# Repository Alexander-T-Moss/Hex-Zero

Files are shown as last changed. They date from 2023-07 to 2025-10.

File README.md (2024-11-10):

# &#x2B22; Hex-Zero &#x2B22; 

At its core, HX0 is a re-design of the [Tri-Zero](https://github.com/zruncho3d/tri-zero) Z motion, with a revised [Pandora Gantry](https://github.com/MasturMynd/Pandora). Without the aforementioned, none of this project would've been possible, so a great amount of thanks is due to [zruncho3d](https://github.com/zruncho3d) and [MasturMynd](https://github.com/MasturMynd) whom indirectly sent me down this rabbit hole!

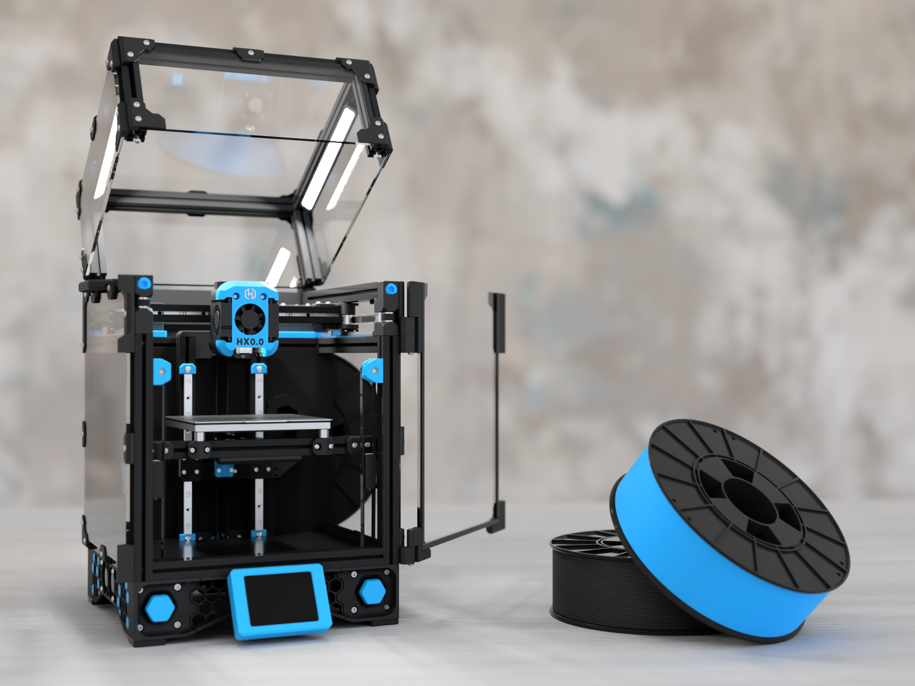
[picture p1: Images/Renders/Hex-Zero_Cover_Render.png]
Hex-Zero_Render


[Latest Release](https://github.com/Alexander-T-Moss/Hex-Zero/releases)

[BOM And Sourcing Guide](https://docs.google.com/spreadsheets/d/1rqf1-H34D0NAQSOrVUcAvukW5k4i_Hs-t34R7qeSDDk/edit?usp=sharing)

~~[Very Early Release Manual](https://docs.google.com/presentation/d/1XJv6mhR6lkI2eAlZ3oS6MfDWln81kRRjcN10jNzyiEM/edit?usp=sharing)~~ (Ignore This, Refer To CAD)

[Common Questions And Answers](https://github.com/Alexander-T-Moss/Hex-Zero/blob/main/QnA.md)

[Community Mods For HX0](https://github.com/Alexander-T-Moss/Hex-Zero/blob/main/Mods)

<br>

## What Differentiates Hex-Zero From Tri-Zero + Pandora Gantry?

When I started working on Hex-Zero, I wanted to address my main concern with Tri-Zero, which was the robustness of the flying bed. I also liked the more honeycomb look of the V0.2 skirts and wanted to incorporate that style into the Hex-Zero skirts. I also noticed some other compatibility issues with how I intended to build things so would need to address them. Below is a summary of some of the major tweaks and changes you'll notice when comparing Hex-Zero to Tri-Zero + Pandora Gantry.

1. Option to either **use bolts** on all bearing stacks **or pins** on all bearing stacks
2. Use **KGLM-03** spherical bearings in the flying bed Z joints (_improve rigidity_)
3. **Reduced Z height of the Z motor mounts** and skirts (_part of the aesthetic changes_)
4. **New front Z tensioners/idlers** to allow clearance with MiniSB (*with additional travel of pandora style gantry*)
5. Optimize printed parts to be **easier to print**
6. **More best-agon hexagons!**

Documentation is another frequently overlooked aspect of projects like these (and by far the most time-consuming thing to complete). When I first started this journey (_before even designing anything_), I had many questions about hardware compatibility, such as "If I do thing A, can I also do thing B", "To do thing C, what do I need for thing D" and "Will doing thing E even work!" To make this project as accessible as possible, I intend to develop documentation and resources that address as many common questions as possible!

<br>

## Community Beta Testing Builds

I want to extend a massive thanks to everyone who took a leap of faith in building and testing this project in its early stages, below is a collage of some HX0s built during the beta testing of this project :)

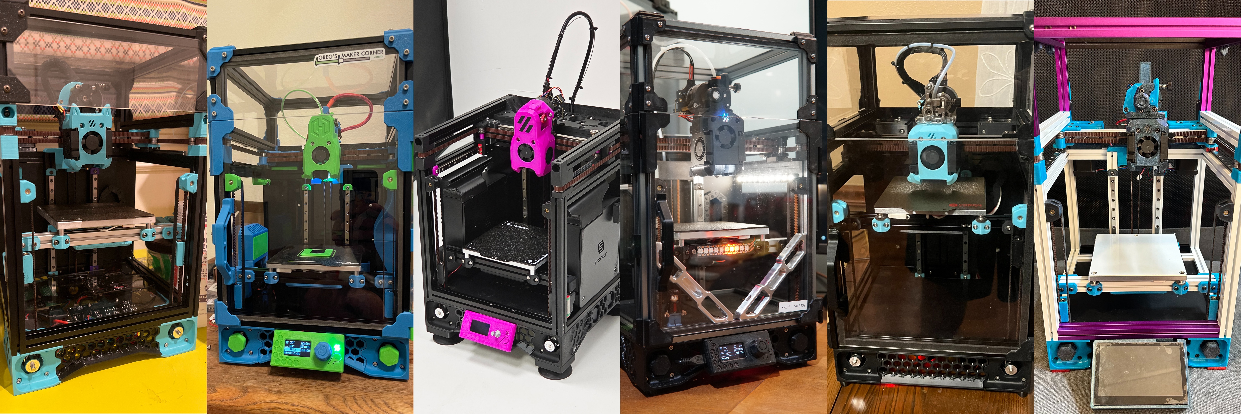
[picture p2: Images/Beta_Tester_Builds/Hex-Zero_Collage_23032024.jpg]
Beta Testing Collage


Credits in order of images left to right: Hud (*HX0.1*),  Rahim Damji (*HX0.2*), Siboor (*HX0.3*), Spicy Pesto (*HX0.5*), Albino Deer (*HX0.4*), Sidjdosjsid (*HX0.ToBe*)

<br>

## Credits

- **[Zruncho3D](https://github.com/zruncho3d)**: Creator of [Tri-Zero](https://github.com/zruncho3d/tri-zero), what started this project
- **[MasturMynd](https://github.com/MasturMynd)**: Designer of the amazing [Pandora's gantry](https://github.com/MasturMynd/Pandora)
- **[Nemgrea](https://github.com/nemgrea)**: For creating [V0.2](https://vorondesign.com/voron0.2), the real root of this project
- **[Chirpy](https://github.com/chirpy2605)**: The brains behind the wonderful [dragon burner](https://github.com/chirpy2605/voron/tree/main/V0/Dragon_Burner) toolhead

If you accidentally stumbled across this project, checkout other similar projects on [3D Printers... For Ants](https://3dprintersforants.com/)

<br>

## Support

With all things, nothing is truly perfect, so if you come across any issues, no matter how small, or find something you think can be improved, please don't hesitate to reach out with suggestions/feedback on the DOOMCUBE discord server in the [dedicated development channel](https://discord.com/channels/825469421346226226/1220161815455989800) for this project!

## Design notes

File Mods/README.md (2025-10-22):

# &#x2B22; Mods & Additions &#x2B22; 

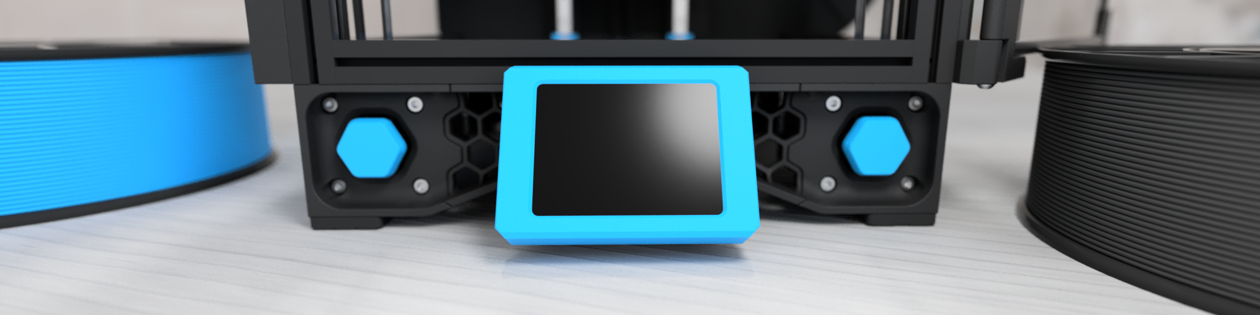
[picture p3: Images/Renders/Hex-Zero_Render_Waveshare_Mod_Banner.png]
Waveshare_Banner_Image


# List Of Mods

| Author | Mod Name | Description |
| --- | --- | --- |
| Alexander T-Moss |  [3mm Panel Clips](/Mods/Alexander_T-Moss/3mm_Panel_Clips) | Allows the use of 3mm foam tape |
| | [Handles](/Mods/Alexander_T-Moss/Handles) | Somewhere to grab onto to lift the printer up |
| | [Full Height Panels](/Mods/Alexander_T-Moss/Full_Height_Panels) | Hard mounted top hat and info on using full height panels (BoxZero esque)|
| | [Bed Fans](/Mods/Alexander_T-Moss/Bed_Fans) | Mounts for 3010 blower fans on the underside of the bed |
| | [Hex Panels](/Mods/Alexander_T-Moss/Hex_Panels) | For if you want more bestagons in your printer |
| | [Skirt Fans](/Mods/Alexander_T-Moss/Skirt_Fans) | Mounts for a pair of 3010's on the side skirts |
| MechaXx |[Waveshare 2.8 Screen](/Mods/MechaXx/Waveshare_28_Screen) | Waveshare 2.8 screen front skirt mount |
| tiramisu |[Serial Plates](/Mods/tiramisu/Serial_Plates) | HX0 Serial Plate for 1515 extrusions |
| Hoeby |[Bottom Wago Holder](/Mods/Hoeby/Bottom-Wago-holder) | Wago Block Holder |
| | [Bottom FT EMS](/Mods/Hoeby/Bottom_FT_EMS) | Bottom FT EMS |
| | [Front belt tensioner](/Mods/Hoeby/Front_Belt_Blocks) | Different belt clamping in front tensioner |
| | [Extended MantaRay kinematic](/Mods/Hoeby/MantaRay%20mount%20with%20extend) | Prevent easelly dropping MantaRay |
| | [HX0_Anthead](/Mods/Hoeby/HX0_Anthead) | AntHead with mods specially for HX0 |
| | [PurgeBucket](/Mods/Hoeby/PurgeBucket) | PurgeBucket to fit Mantaray and Hammerhead bed |
| | [SuperSlicer](/Mods/Hoeby/SuperSlicer_Texture_Model) | Files to customize your SuperSlicer to HexZero |
| | [MantaRay KGLM03 joints](/Mods/Hoeby/MantaRay%20with%20KGLM03%20joints) | MantaRay bed with KGLM03 ball joints |
| MJ26gaming | [4010 Bed Fan](/Mods/MJ26gaming/Hex%204010%20Bed%20Fan) | Mount for dual 4010 bed fans |
| G |  [Hex-Burner Revo PZ](/Mods/G/Hex-Burner_Revo_PZ) | STLs for routing and mounting the Revo PZ |
| |  [Hex-Burner Offset Carriage](/Mods/G/Hex-Burner_Offset_Carriage) | X-Carriage to offset the Hex-Burner toolhead 2mm forward |
| |  [Top Hat Braces](/Mods/G/Top_Hat_Braces) | A collection of STLs to permanantly secure the top hat |
| |  [GBB15 Motor Panel](/Mods/G/GBB15_Motor_Panel) | GBB15 motor panel mount |
| fronti90 |[48mm Z Motors](/Mods/fronti90/48mm_z_motors) | Mounts and skirts for 48 mm Z Motors |

<br>
<br>
<br>

# Information For Adding A Mod
Below is a quick summary of changes required for submitting a mod to the mods folder

## Table Structure
Information for updating the table for the addition/modification of a mod
- Put the name of the mod hyperlinked to the location of the mod in the repo
- A short single-sentence description of the mod
- Your name as the author

Example table entry: `| Your Name Here |  [Mod Folder Name](Link_To_Mod_Folder) | Short Description |`

## Folder Structure
Information for updating the `Mods` folder for the addition/modification of a mod

The `Mods` folder uses a 2 layer folder structure to organize all the mods
1. `Author Folder` - Top-level folder where all of an author's mods are
2. `Mod Folder` - The folder for an individual mod, which will be found in its relevant `Author Folder`

### Example Of Mod Folder Structure

| `Mods` Folder | `Author Folder` | `Mod Folder` |
| --- | --- | --- |
| Mods | Person 1 | Mod A From Person 1 |
|  |  | Mod B From Person 1 |
|  |  | Mod C From Person 1 |
|  | *Person 2 | *Mod D From Person 2 |
|  | Person 3 | Mod E From Person 3 |
|  |  | Mod F From Person 3 |

_*Note: If someone has a single mod it still has an author folder_

## What Must A Mod Folder Need To Include
At a bare minimum, each mod folder should contain a CAD file (_ideally a .step and/or .f3d file_), STLs (_ideally oriented correctly for printing_) a **screenshot from CAD or a photo** of the mod installed and a short `README.md` providing the relevant information for the mod

Also, make sure there are no spaces in any file or folder name (_using underscores `_` or dashes `-` where required_)

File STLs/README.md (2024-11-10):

# &#x2B22; Printing Guide &#x2B22; 

Below you'll find information on recommended print settings, how to slice MMU parts, etc.

<br>

## Recommended Print Settings
All printed parts where possible are designed with the following print settings in mind.

> Material: `ABS/ASA` (_Or Better_)
>
> Perimeters: `4`
>
> Top/Bottom Layers: `5`
> 
> Infill: `40% Cubic`
> 
> Layer Height: `0.2mm` (_Incl. First Layer_)
> 
> Extrusion Width: `0.4mm Forced` (_Just For Internal/External Perimeters_)

<br>

## Optional Multi-Material Parts
Where applicable, there are `.step` files for parts that can be printed in multiple colours. They are often located in a folder of the part name along with an `.stl` of the part.

> After importing them into your slicer of choice, if they don't already show as multiple parts, right click on the object and split it into parts (not objects!).
>
> Also worth noting the `.step` version of parts are not oriented so you may need to refer to the `.stl` for correct orientation.

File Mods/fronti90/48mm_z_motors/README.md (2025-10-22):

# &#x2B22; 48mm Z Motors &#x2B22;
Mounts and skirts for 48 mm Z Motors (e.g. 17HS19-2004S1)

Additionally you will need to change your electronics setup. For me mounting the PSU at the bottom (at an angle) and all other electronics on the back worked best.

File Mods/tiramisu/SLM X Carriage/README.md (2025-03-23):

# HexMetal
Toolhead carriage designed for SLM printing and use in the Hex Zero printer for ants or any other front-facing MGN9H rail printer.

This is heavily based on the **incredible** work Alex has done designing the Hex Zero.

~~Currently awaiting the first prototype by PCBWay :)~~
~~Received, belt path needs to be widened but all else is OK. New ETA: When I receive and test new part :)~~

Revised version received and test fitted. Minor tweaks made based on use.
Files have now been uploaded. **Highly advised** that you print in FDM first and consider how SLM tolerances would change the fit you get.

I have uploaded version with both a mounting for normal Dragonburner (and similar) as well as Alex's Dragonburner for Hex Zero.

This render is not fully indicative of the STLs, will update soon.

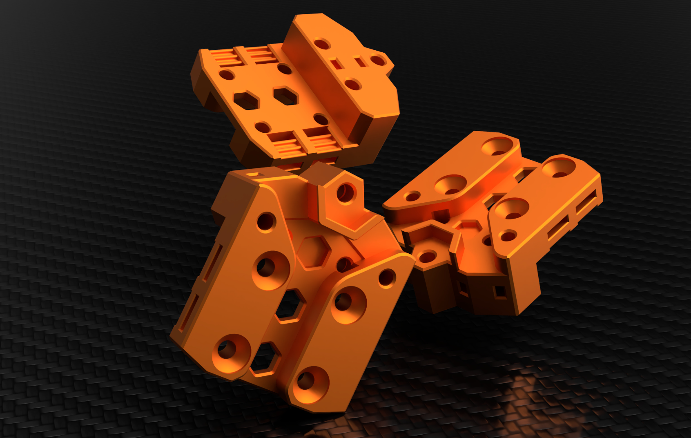
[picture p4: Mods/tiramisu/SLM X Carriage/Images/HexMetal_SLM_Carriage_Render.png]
Render of HexMetal, same part, shown thrice from different angles


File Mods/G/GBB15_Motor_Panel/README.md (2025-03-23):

# GBB15 Motor Panel Mount

This mod mounts the GBB15 in place of the motor panel. The board is mounted so that the MCU and motor drivers can be heat sinked into the chamber. The Bowden tube and CAN harness can be zip tied in place through the hexagon hole into the chamber. Two M3 heatset inerts are required mount the GBB15 to the panel.

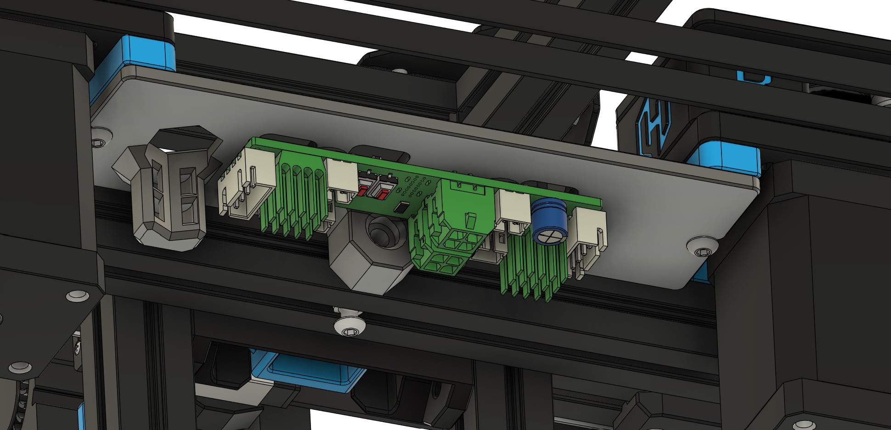
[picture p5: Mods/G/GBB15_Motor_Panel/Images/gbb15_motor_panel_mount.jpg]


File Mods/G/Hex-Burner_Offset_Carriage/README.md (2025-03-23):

# Offset X-Carriage for Hex-Burner

This mod offsets the placement Hex-Burner toolhead 2mm forward. A support piece is included in the STL, and can be removed after printing.

The intent of offsetting the toolhead is for: 
- Routing of all toolhead wires in the carriage channel.
- Clearing the Pi Camera with using the popular Voron 0 Raspberry Pi Camera Mount by johanncc. Depending on the size of the camera PCB, the mount corner of the PCB may need to be trimmed. 
- Allowing excees belt to extend out the side of the carriage without affecting toolhead alignment. 

The disadvantage to this mod is that you will lose 2mm of Y-axis travel; however, this is negligible in many cases, especially if you are using the mini-fridge door mod.

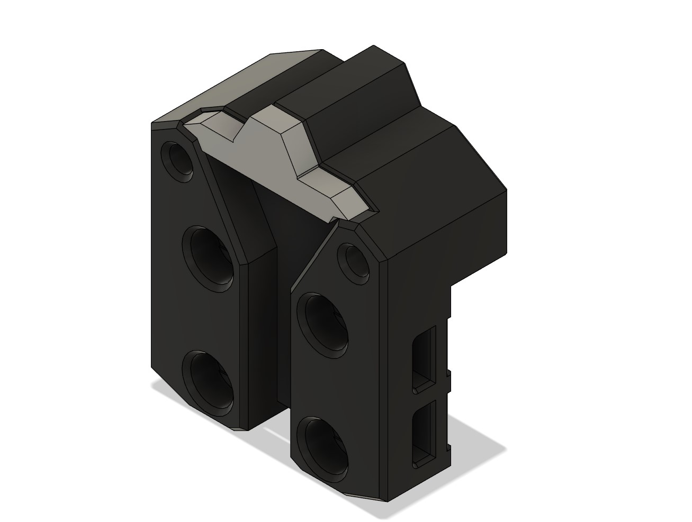
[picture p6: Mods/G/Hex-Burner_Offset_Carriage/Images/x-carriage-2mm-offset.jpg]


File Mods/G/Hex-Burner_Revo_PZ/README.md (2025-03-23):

# Revo PZ Mods for Hex-Burner

This is a set of STLs to use the Revo PZ with the Hex-Burner. 

## Hex-Burner Revo PZ Sherpa Mount
The Revo PZ Sherpa Mount is used to provide a routing path of the PZ's flex cable through the top and out of the back of the toolhead. This part is compatible with the Hex-Burner's fastener spacing and any Sherpa style extruder.

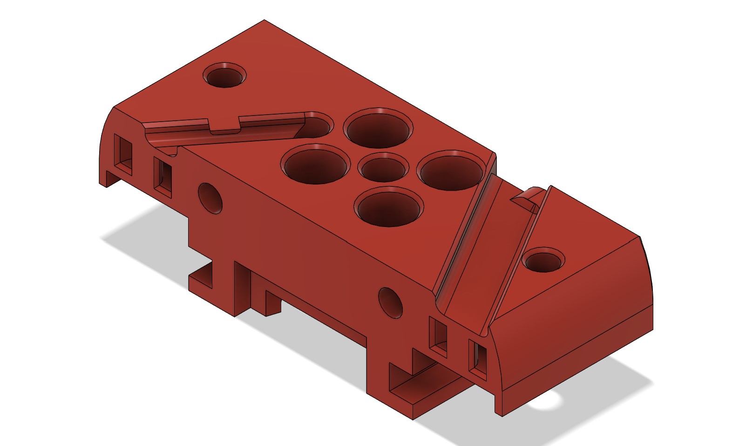
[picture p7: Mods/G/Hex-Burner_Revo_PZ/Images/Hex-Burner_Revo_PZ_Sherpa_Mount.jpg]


## X-Carriage Revo PZ Board Mount
The X-Carriage Revo PZ Board Mount is used to mount the PZ's breakout board on top of the Hex-Burner X-Carriage and under the extruder motor. Optionally, there is a version with an extended X-axis bumper and zip-tie point for the hot end wires. The bumper is placed to impact the XY joints during sensorless homing. This mount will require the top toolhead screw to be 2mm longer. Two M3 heatset inerts can be added for an attachment point with toolhead MCU mounts. The image below shows the Maple Leaf Makers EBB36 interfacing with this mount.

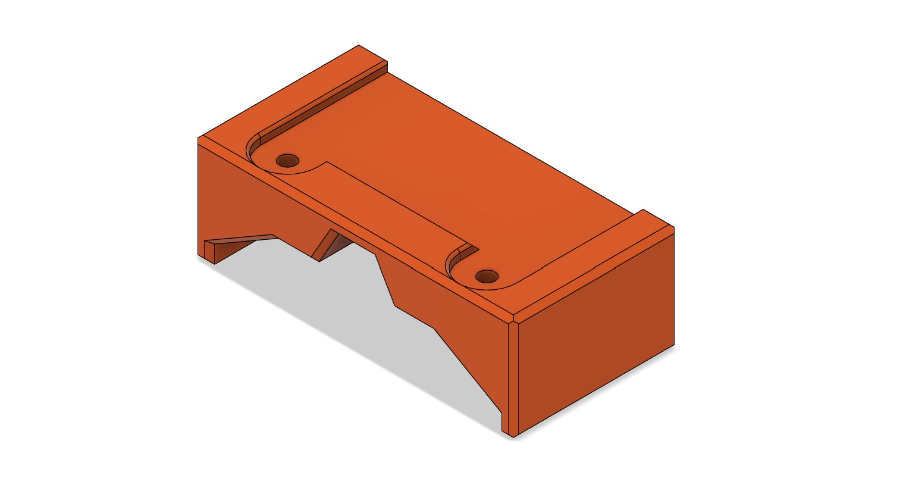
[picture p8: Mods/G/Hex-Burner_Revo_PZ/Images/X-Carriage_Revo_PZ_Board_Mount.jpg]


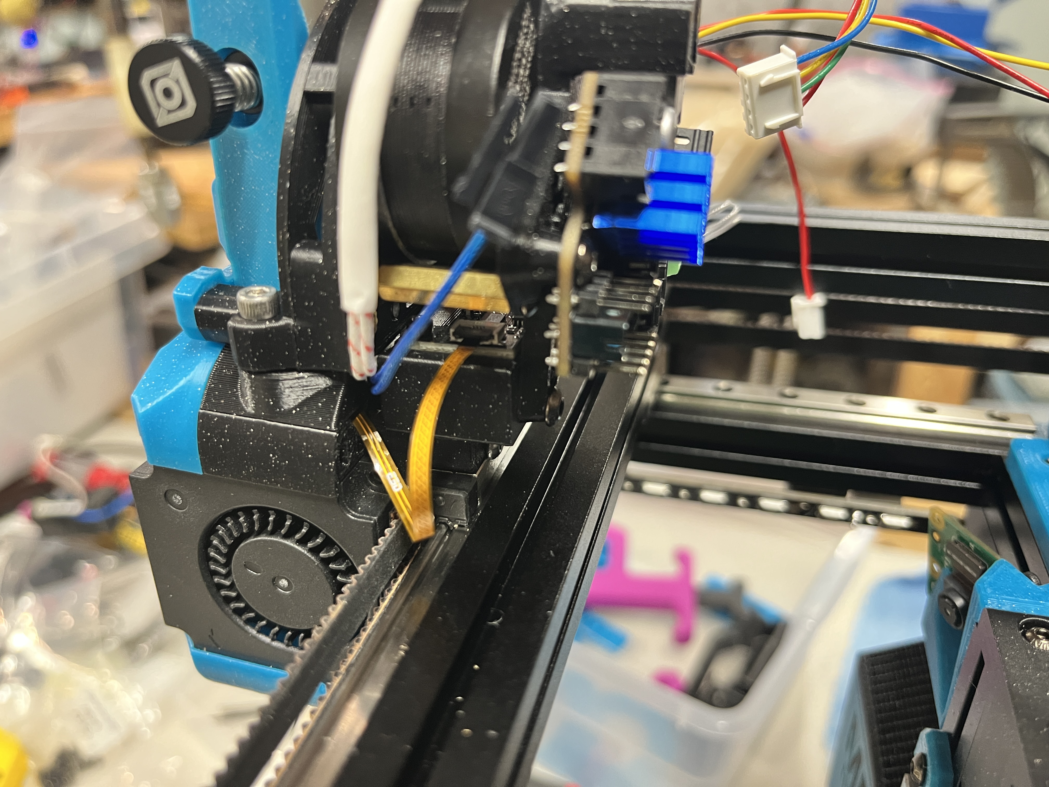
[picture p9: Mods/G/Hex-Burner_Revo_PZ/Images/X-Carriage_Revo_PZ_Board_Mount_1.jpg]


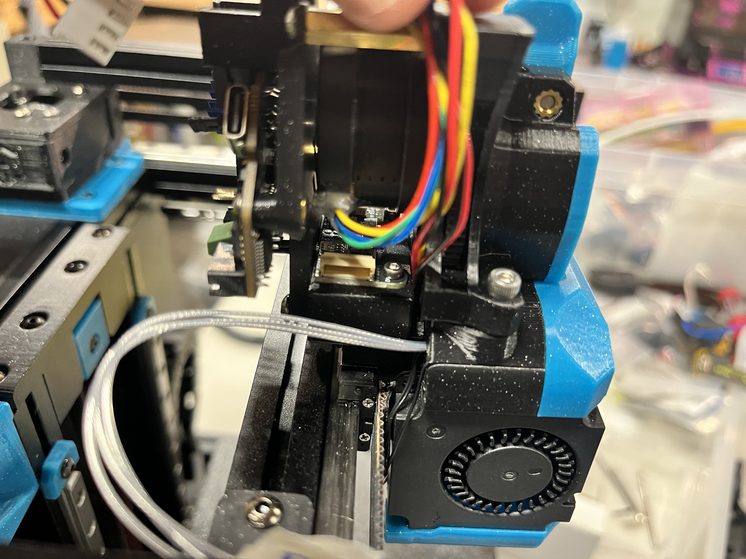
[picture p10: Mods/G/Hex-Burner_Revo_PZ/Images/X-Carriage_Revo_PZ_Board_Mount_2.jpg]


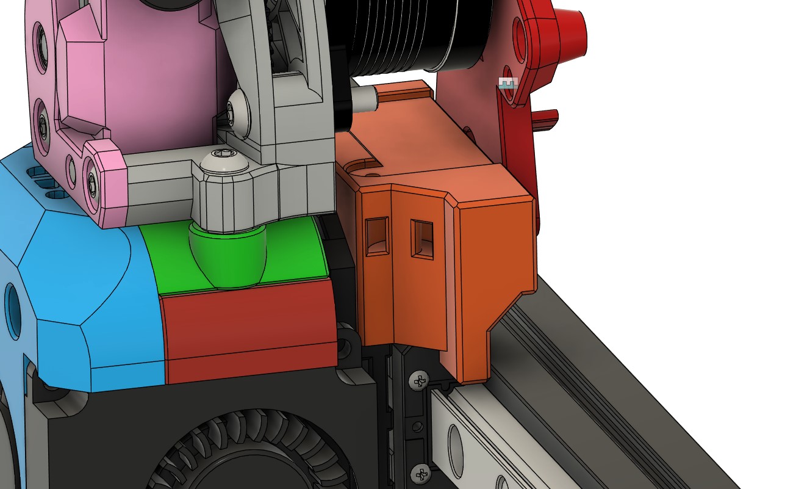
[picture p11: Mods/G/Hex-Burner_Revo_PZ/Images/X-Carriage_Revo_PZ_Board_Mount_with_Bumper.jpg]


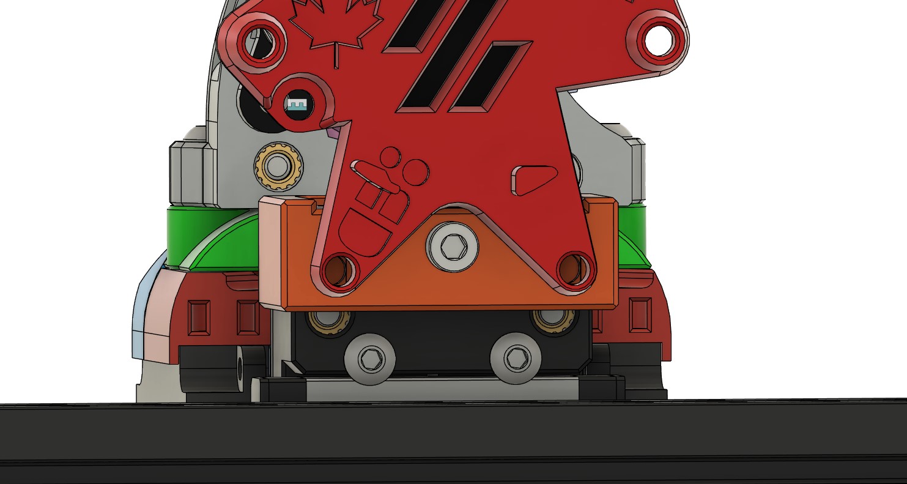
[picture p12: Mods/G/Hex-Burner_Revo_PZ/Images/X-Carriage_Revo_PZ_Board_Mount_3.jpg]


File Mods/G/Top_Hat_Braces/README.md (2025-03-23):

# Top Hat Braces

This mod is a colletion of STLs to secure the top had to the printer.

The corner brace with 2mm offset can be used for mini-fridge mod users needing to extend the height of the top hat. Additional nuts will need to be preloaded into the top hat extrusions.

The rear brace interfaces with existing mount points and had a slot for the Voron0 rear panels.

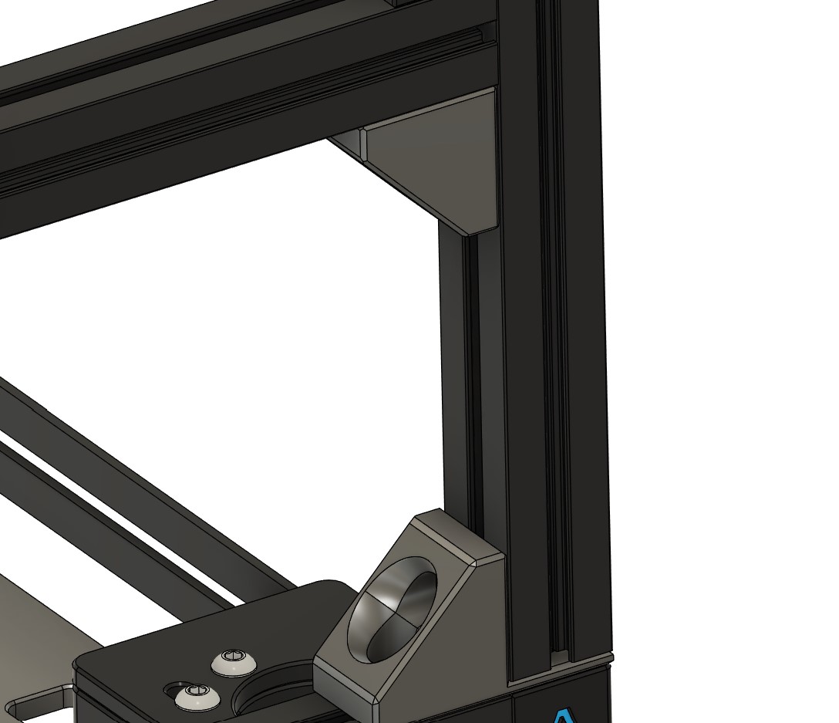
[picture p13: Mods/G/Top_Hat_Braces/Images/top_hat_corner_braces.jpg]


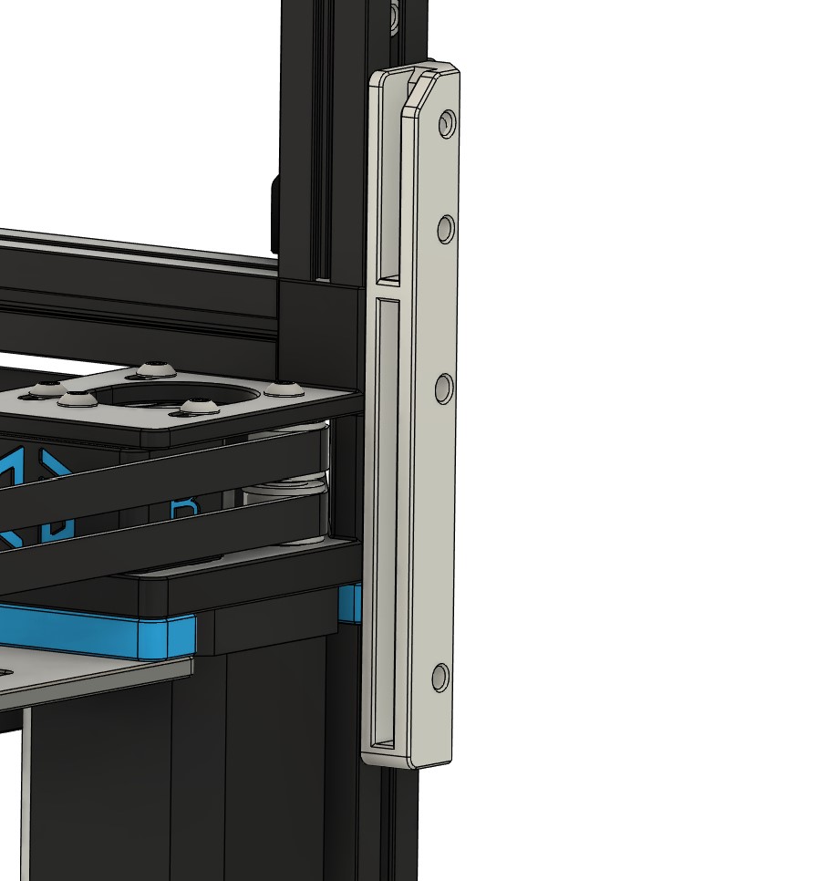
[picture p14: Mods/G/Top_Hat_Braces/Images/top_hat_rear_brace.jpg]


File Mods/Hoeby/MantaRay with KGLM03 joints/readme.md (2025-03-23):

# &#x2B22; HX0 MantaRay bed with KGLM03 ball joints &#x2B22;
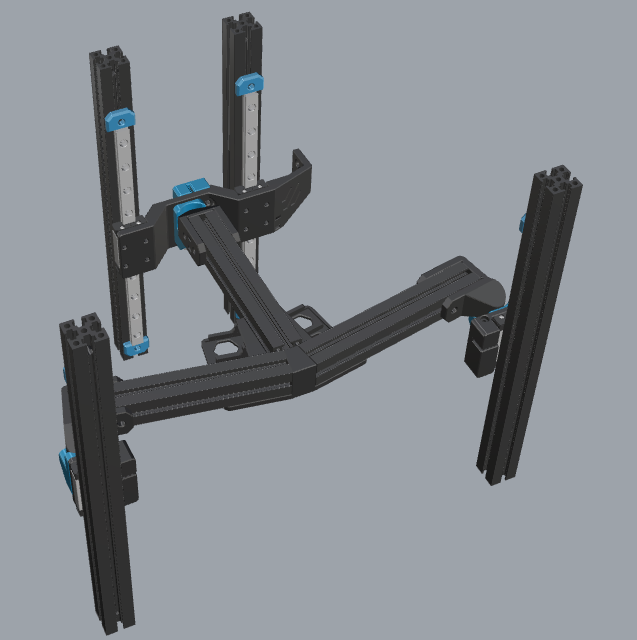
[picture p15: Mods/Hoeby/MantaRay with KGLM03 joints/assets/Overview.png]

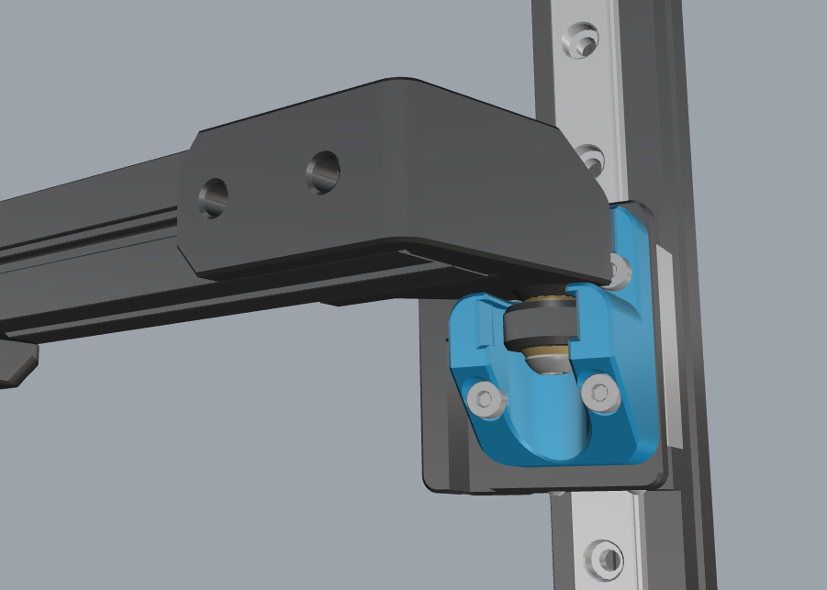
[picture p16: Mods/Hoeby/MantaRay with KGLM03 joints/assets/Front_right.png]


# Mod Guide
The MantaRay uses the stock 3x 100mm extrusions from a V0 kit. <br>
Original the MantaRay uses rail mounts with pins, they are easier to source then the KGLM03 joints. <br>
This mod uses the KGLM03 joints from the Hammerhead bed, on the MantaRay bed.

## What are the changed parts in this mod:
- [a]_kinematic_rail_front_left.stl
- [a]_kinematic_rail_front_right.stl
- [a]_kinematic_rail_rear.stl
- front_left_gantry_attachment.stl
- front_right_gantry_attachment.stl
- rear_gantry_attachment.stl

## Needed parts
- 3x KGLM-03
- 2x M2x8
- 4x M2x10
- 2x M2x15
- 4x M2x16
- 3x M3x10
- 3x Heat insert (voron size)

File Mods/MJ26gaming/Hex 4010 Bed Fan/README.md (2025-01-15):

# Dual 4010 Axial Bed Fan Mount for Hex Zero

## About this mod
This replace's the mod Alexander made, allowing for even more CFM for chamber heating. <br>
It definitely works with the Hammerhead bed. I have not tested it on the Manta Ray but it probably works there too. <br>
I use GDStimes, I will update with the lifespan of those. <br>
Consider usinga stronger bed heater. The BOM 60w heater will definitely be overcooled by this. I use a 120w heater.

## Filament
I reccomend using you highest temp filament for this. <br>

## Hardware needed for this mode
- 2x M3x8
- 8x M3x12
- 8x M3 Heatset Inserts

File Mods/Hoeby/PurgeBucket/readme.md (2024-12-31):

# PrugeBucket for HexZero, mantaray and hammerhead bed compatible
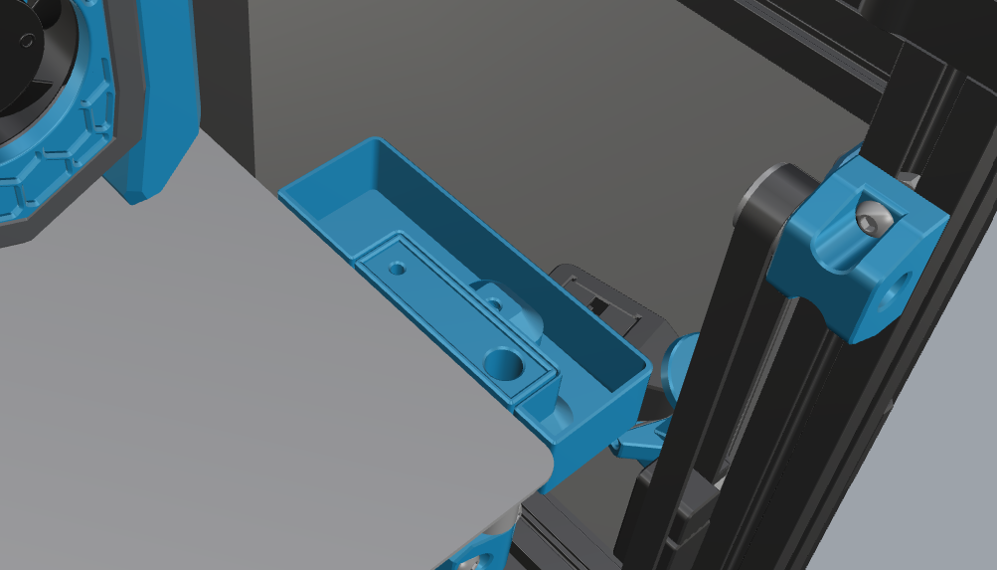
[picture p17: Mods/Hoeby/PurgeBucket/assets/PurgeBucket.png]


## Which 3d parts are shared
Only the 3D printed parts for the PurgeBucket are shared. <br>
The bed-mount is mantaray and hammerhead bed compatible.

## Hardware needed for this mode
- 2x M3x8
- 2x M3 nut
- 2x Magnet 6x3
- 1x Nozzle silicone brush (Bambu A1)

## Printing advice
The advice is to print the bucket with support. <br>
There isn't a drawn support in the file. <br>
Without a support, the magnet hole for the bucket could be deformed.

## Used klipper macro
This macro is used to clean the nozzle. <br>
```
[gcode_macro CLEAN_NOZZLE]
variable_start_x: 128
variable_start_y: 55
variable_start_z: 3.6
variable_wipe_dist: 45
variable_wipe_count: 5
variable_wipe_speed: 10000
variable_raise_distance: 20

gcode:
 ## Check if extruder has minimum extrude temperature, otherwise heat extruder
 {% set temp_to_low = False %}
 {% set temp_min = printer.configfile.settings["extruder"].min_extrude_temp|float %}  

 ## Check if the target that is set on the extruder is larger then minimum extruder temp
 ## Otherwise heatup to minimum extruder temp
 {% if printer.extruder.target < temp_min %}
    M104 S{temp_min}
    {% set temp_to_low = True %} 
 {% endif %}
 
 ## Check if homing is done, otherwise homing
 {% if "xyz" not in printer.toolhead.homed_axes %}
   G28
 {% endif %}

 ## Check if Z_Tilt is done, otherwise Z_Tilt_Adjust
 {% if printer.z_tilt.applied == False %}
   Z_TILT_ADJUST
 {% endif %}

 ## There was no extruder target, waiting for extruder to finish heating to minimum extruder temp
 {% if temp_to_low == True %}
   M109 S{temp_min} 
 {% endif %}

 G90                                            

 ## Move nozzle to start position
 G1 X{start_x} Y{start_y} F{wipe_speed / 2}
 G1 Z{start_z} F1500

 ## Wipe nozzle
 {% for wipes in range(wipe_count) %}
    {% for coordinate in [(start_x, start_y),(start_x, start_y - wipe_dist)] %}
        G0 X{coordinate[0] - 0.6 * wipes} Y{coordinate[1]} F{wipe_speed}
    {% endfor %}
 {% endfor %}

 ## There was no extruder target, disable extruder heater
 {% if temp_to_low == True %}
   M104 S0 
 {% endif %}
  
 ## Raise nozzle
 G1 Z{raise_distance} F1500
 G1 X60 Y60 F{wipe_speed / 2}

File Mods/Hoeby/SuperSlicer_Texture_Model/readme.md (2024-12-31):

# HexZero texture and model for SuperSlicer
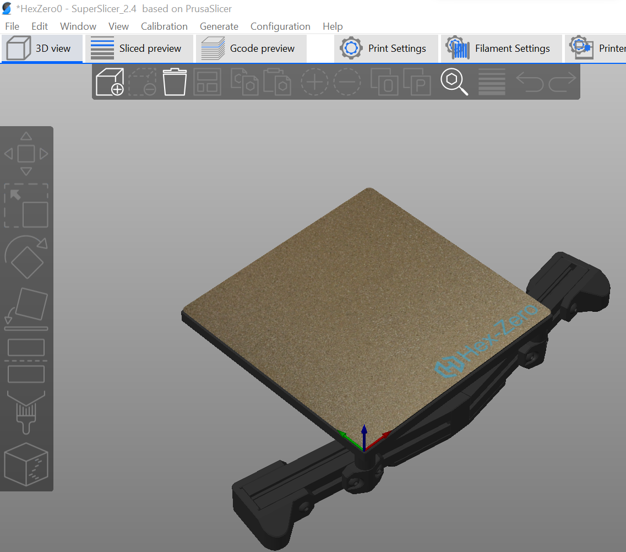
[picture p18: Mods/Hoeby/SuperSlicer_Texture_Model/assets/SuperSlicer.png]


This is not a 3d mod, but files to import the HexZero into your SuperSlicer <br>

## How to change to bed + sheet in SuperSlicer
- Open SuperSlicer <br>
- Go to <b>Printer settings</b>
- Choose <b>General</b>
- Choose <b>Set</b>
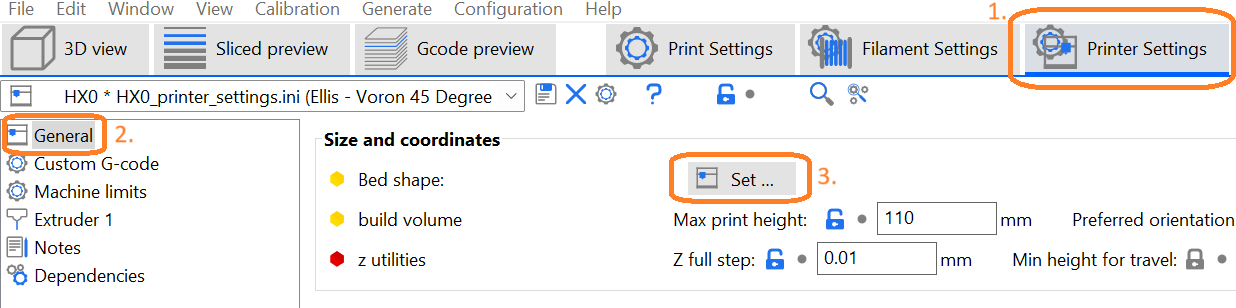
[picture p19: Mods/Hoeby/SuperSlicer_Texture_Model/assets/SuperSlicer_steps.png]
 <br>
<br>
- A option <b>Texture</b> choose <b>Load</b> and search for the .png file <br>
- A option <b>Model</b> choose <b>Load</b> and search for the .stl file <br>
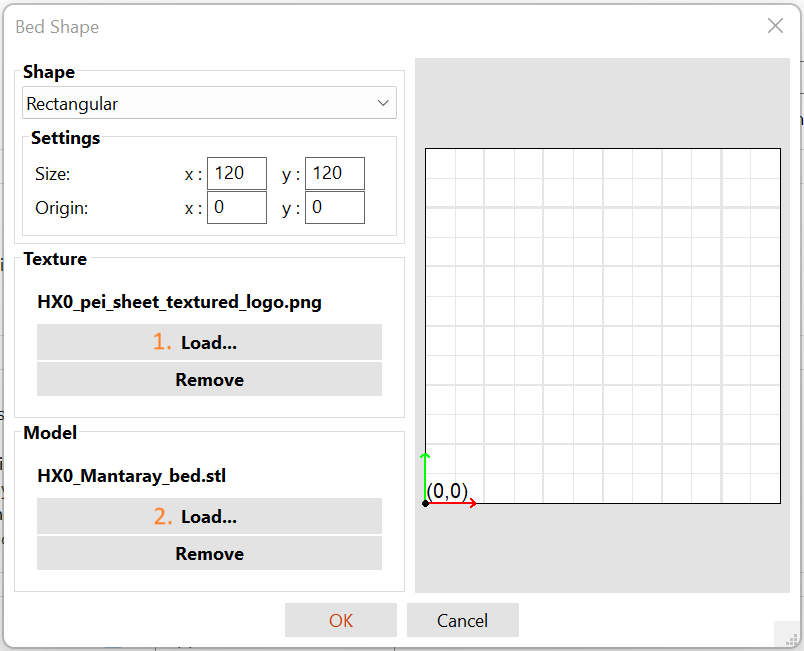
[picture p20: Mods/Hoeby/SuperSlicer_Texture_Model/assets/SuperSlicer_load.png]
 <br>

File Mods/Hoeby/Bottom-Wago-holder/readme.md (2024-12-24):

# Wago-mount special for HexZero

## The idea about this mod
There a nice space next the the Z-extrusions, which this mod will fill up with a wago mount. <br>
The holder has place for:
- 2x Wago 3-pin
- 2x Wago 5-pin

## Which 3d parts are shared
Only the 3D printed parts for the wago-mount are shared. <br>

## Hardware needed for this mode
- 2x M3x8
- 1x M3 nut

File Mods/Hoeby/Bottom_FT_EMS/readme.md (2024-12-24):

# FT_EMS_Bottom special for HexZero

## The idea about this mod
The idea is found here; https://www.printables.com/model/553387-ft-ems-voron-v02-v2-electronics-management-system <br>
Just made it compatible for the bottom of the HexZero

## Which 3d parts are shared
Only the 3D printed parts for the EMS bottom are shared. <br>

## Hardware needed for this mode
- 14x M3x8
- 10x M3 nut

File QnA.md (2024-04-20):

# &#x2B22; Questions And Answers &#x2B22;
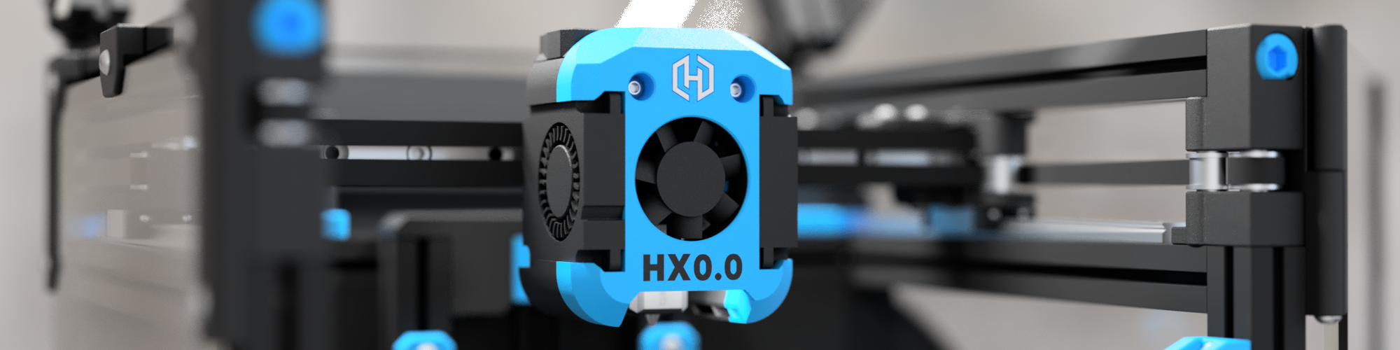
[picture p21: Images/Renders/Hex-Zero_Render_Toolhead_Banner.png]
Hex-Zero_Banner_Image


## How Much Does It Cost To Convert My V0 To A HX0?
Approximately **£100/$125/€115** to **£150/$190/€175**. You may be wondering why there is such a wide range. The cost is entirely dependent on what you already have and how Gucci you want to be when purchasing parts, but you can convert a V0 to a HX0 for somewhere in this range (_conservative estimate_), if not less!

## What Probe Should I Use With My HX0?
There are a few probe options to choose from, all with pros and cons and options depending on what tool head you are using but all need the same general considerations when deciding what is best for your HX0 build!

1. Where is the probe going to dock (_if applicable_)? - Ideally, the dock should put the probe out of the way of the tool head during normal printing. Thanks to the additional XY travel from the Pandora-style gantry in HX0, you get a bit more freedom in probe dock placement. I recommend using a probe mount dock that situates the probe in the rear left corner (_looking into the printer_)

2. How does the probe attach to the tool head (_if applicable_)? Will the additional parts for where the probe attaches to the tool head cause areas where parts will collide when the tool head moves? The main area to pay consideration to is the rear vertical z extrusions. You can often configure the printer in a way to avoid this area to prevent a possible collision

Below is a table detailing some probe and dock combinations and a short pro/con summary for them

| Toolhead Compatibility | Probe | Dock | Pro | Con |
| --- | --- | --- | --- | --- |
| DB & MiniSB | [Klicky]() | [Multple Options](https://github.com/jlas1/Klicky-Probe/tree/main/Printers/Voron/v0#probe-dock-mounts-1) | Well-Documented and community tested | May reduce useable print area and requires homing to front left corner |
|  | [SlideSwipe](https://github.com/chestwood96/SlideSwipe) | N/a | No issues with travel restrictions/collisions | More complex than other probes and needs additional hardware |
| DB Only | [ZeroClick](https://github.com/zruncho3d/ZeroClick?tab=readme-ov-file) | `Centre` | Nice dock position | Toolhead mount may collide with rear z verticle extrusions |

It's also worth noting that HX0 is designed and tested with DB in mind and not MiniSB, so your mileage with MiniSB may vary. Also, each of the recommended probe's pro/cons above assumes using the DB cowl with its respective probe mount

## Do I Need To Buy Extra Extrusion?
Technically, no, but I dislike wording things like that, so allow me to explain. 

If you have a V0 with an extrusion bed, you can build the flying bed using the stock V0 bed extrusions and a printed placeholder at the back of the printer. However, LDO has begun shipping kits with a kirigami and no bed extrusions, which means you will need to source at least one 100mm and one 200mm (or just three 100mm) extrusions for the flying bed in this case, as well as an additional 200mm extrusion for the printer's rear or use the printed place holder.

All that being said, the stock V0 extrusion bed is made up of three 100mm extrusions, and ideally, you want to use a single 200mm instead of two 100mm on the front of the flying bed, so you may still need to source 200mm extrusions for the flying bed and while you're at it, get one for the back of the printer. I should also clarify that the additional rear extrusion is not structural and is only there to make mounting skirts easier at the back of the printer!

Fortunately, these additional extrusions are in lengths that can typically be found pre-cut and tapped

## Do I Need To Drill Holes In The Existing V0 Extrusions?
If you want to mount the rear extrusion, drill two holes to accommodate it. With the printed placeholder, however, you can avoid drilling holes, but I strongly advise you to drill the necessary holes.

There is a jig included to drill the holes, making it rather simple, and because these holes are only to allow an Allen key through to tighten a blind joint bolt, they do not need to be accurate, so there is no need to go for sub-mm or anything silly precise with them!

## Can I Serial A HX0 As a V0?
**Yes**. HX0s can be serialised as a V0 (_assuming you are not converting an existing serialised V0_) while also receiving a HX0 serial to display on the printer!

# Still Got Questions?

Please feel free to reach out on the [dedicated development channel](https://discord.com/channels/825469421346226226/1220161815455989800) for this project in the doomcube discord server!

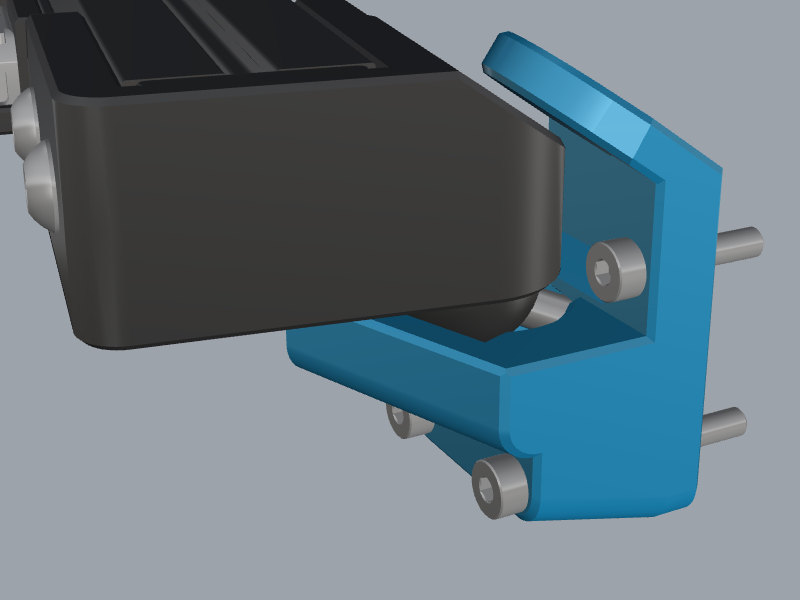
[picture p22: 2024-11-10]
Mods/Hoeby/MantaRay mount with extend/assets/Front Left image.png

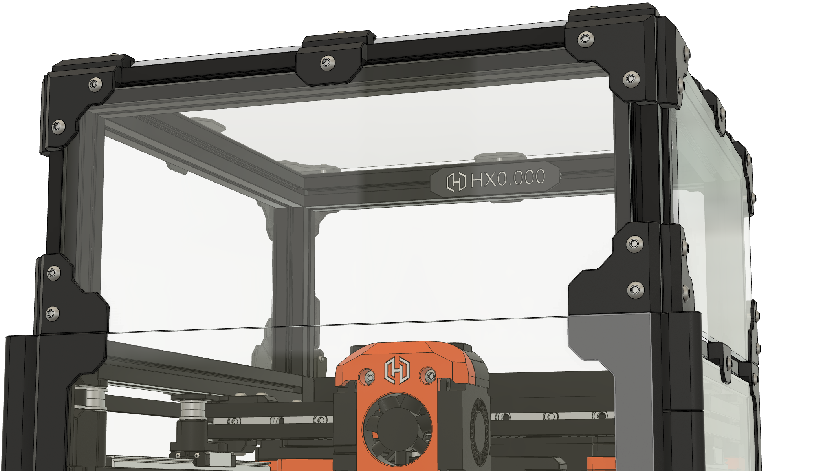
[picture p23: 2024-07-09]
Mods/tiramisu/Serial_Plates/Images/Hex-Zero_Render_Serial_Plate.png

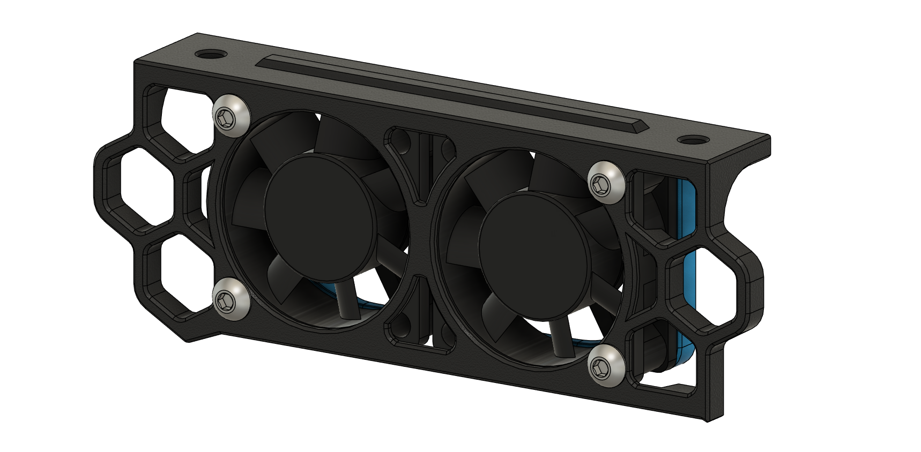
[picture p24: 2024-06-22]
Mods/Alexander_T-Moss/Skirt_Fans/Images/Skirt_Fans.png

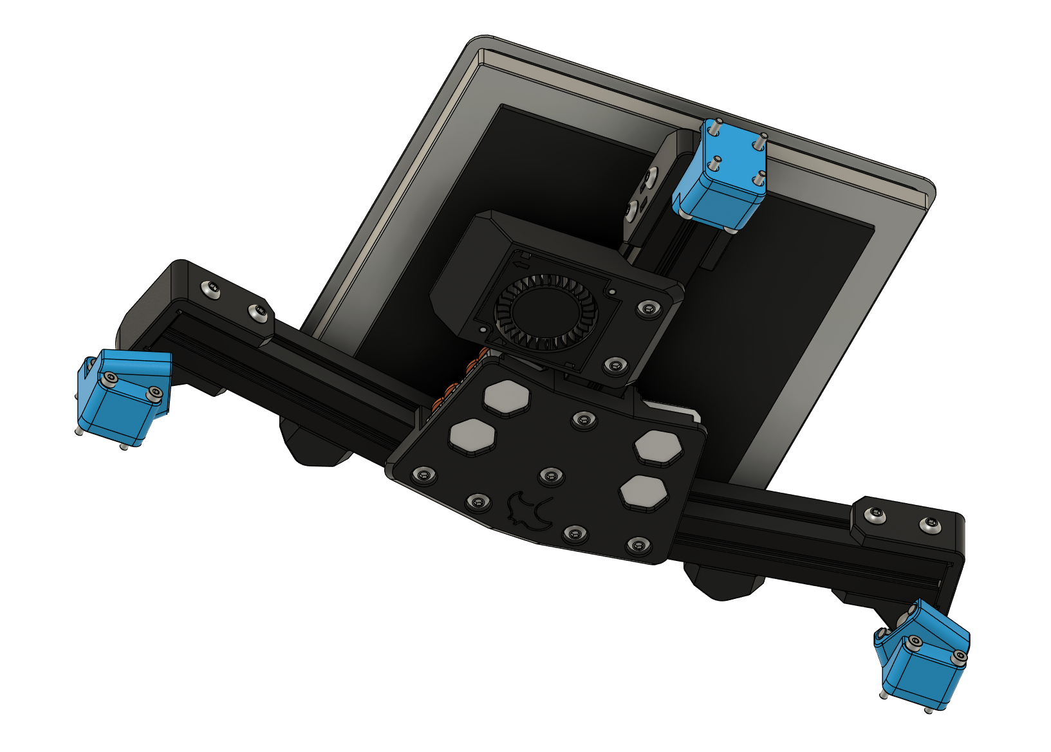
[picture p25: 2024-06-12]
Mods/Alexander_T-Moss/Bed_Fans/Images/single_fan_rear.png

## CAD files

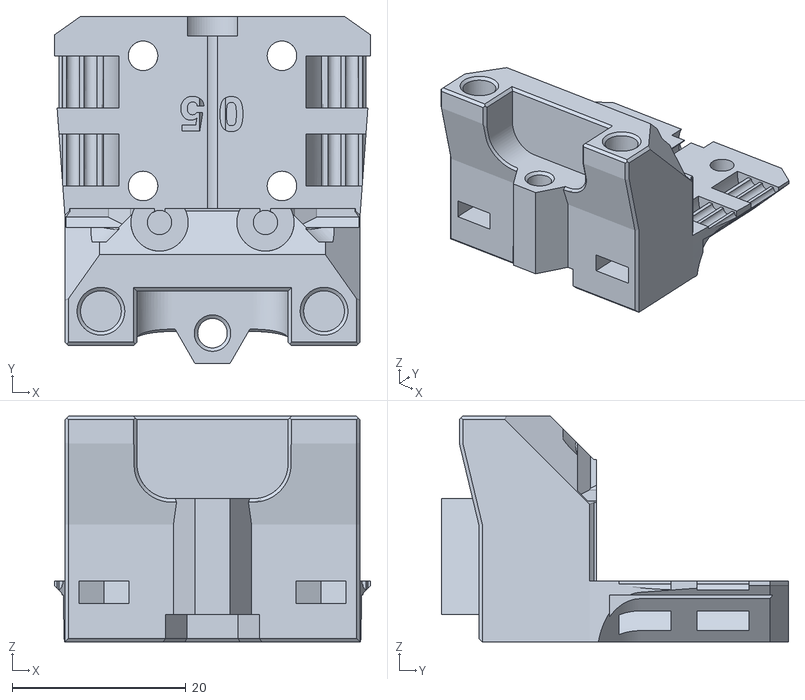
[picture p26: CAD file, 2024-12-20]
Mods/Hoeby/HX0_Anthead/STLs/Carriage/HX0_AntHead_Assembly_v43_x_carriage_x1.stl
36.4 x 40.0 x 26.0

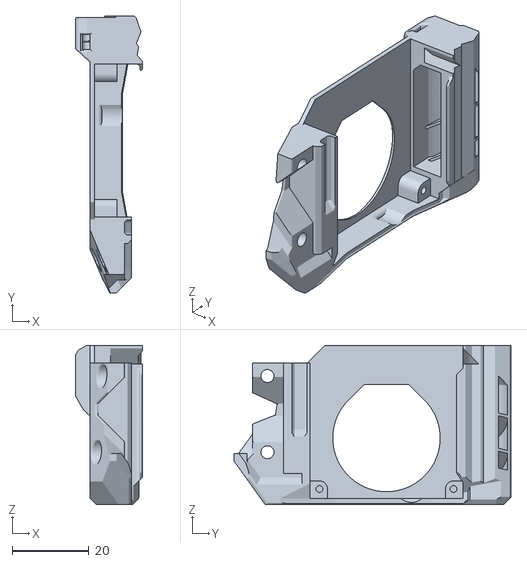
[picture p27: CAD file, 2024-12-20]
Mods/Hoeby/HX0_Anthead/STLs/Ducts/[a]_HX0_AntHead_Assembly_v43_left_duct_x1.stl
17.6 x 72.3 x 41.6

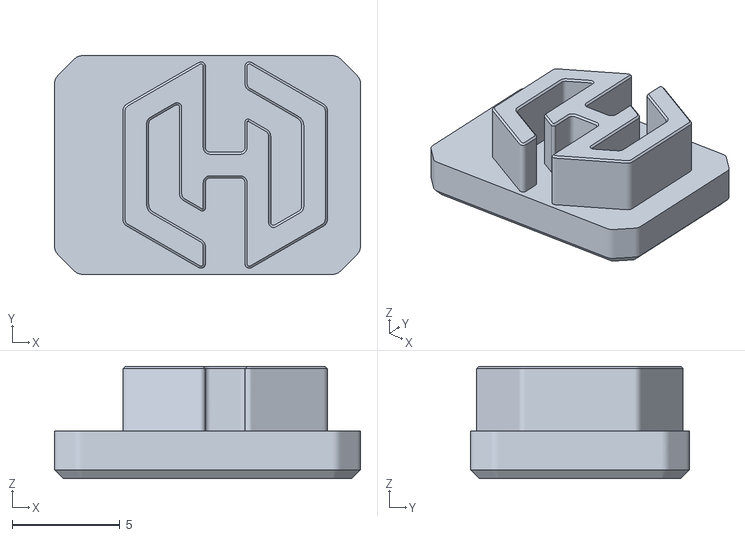
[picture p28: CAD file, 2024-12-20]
Mods/Hoeby/HX0_Anthead/STLs/LEDs/HX0_AntHead_Assembly_v43_led_diffuser_x1.stl
14.2 x 10.1 x 5.20

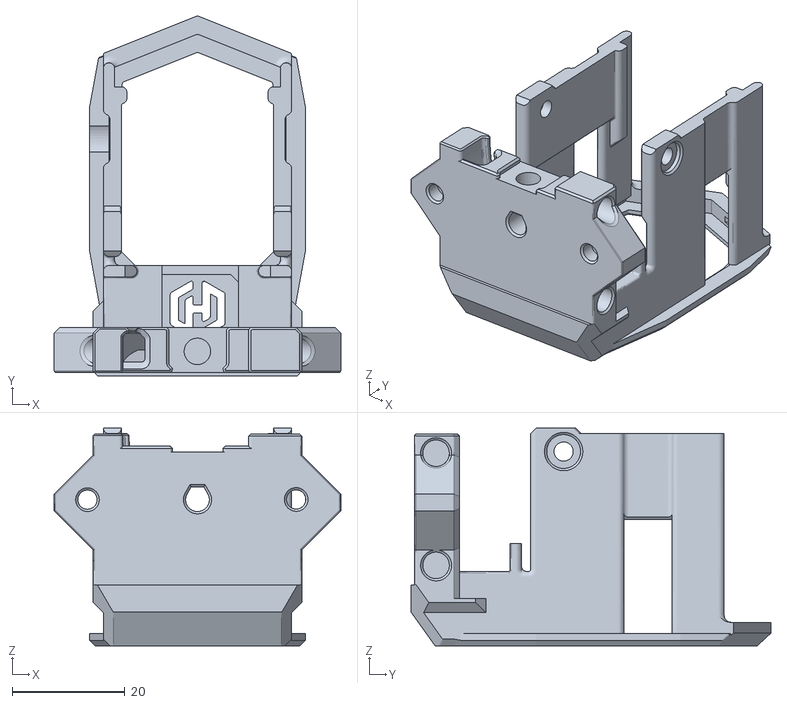
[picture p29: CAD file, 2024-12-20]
Mods/Hoeby/HX0_Anthead/STLs/Main_Bodies/HX0_AntHead_Assembly_v43_main_body_O2_x1.stl
50.8 x 63.8 x 38.6

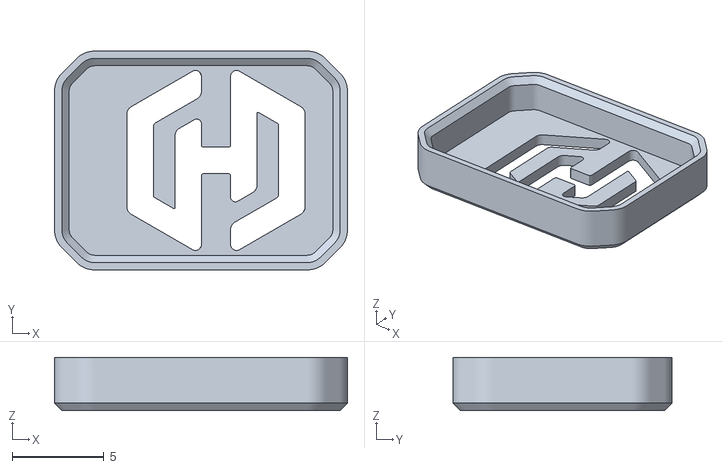
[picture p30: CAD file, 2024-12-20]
Mods/Hoeby/HX0_Anthead/STLs/LEDs/HX0_AntHead_Assembly_v43_led_light_shield_x1.stl
16.0 x 11.9 x 2.90

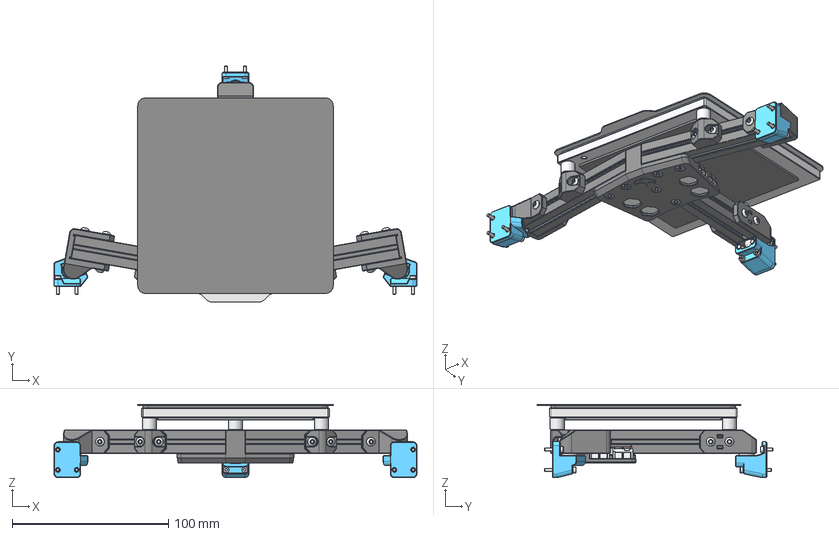
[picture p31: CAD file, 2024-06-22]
CAD/Flying_Beds/Manta-Ray/Manta-Ray_Bed.step
232.0 x 150.9 x 46.9 mm
rear_gantry_attachment
front_left_gantry_attachment
front_right_gantry_attachment
front_bed_mount_2x x 2
[a]_kinematic_rail_front_left
[a]_kinematic_rail_rear
[a]_kinematic_rail_front_right
centre_bed_brace
1515 100mm - F x 3
M3x8 BHCS x 20
M3x16 BHCS x 3
M3x12 WFHS x 3
M2x18 SHCS x 6
M2x6 SHCS x 2
M2x10 SHCS x 2
M3 Hexnut x 21
M3 Threaded Insert x 5
Aluminium Bushing 8mm x 3
Magnet Sheet
MIC6 Plate
Spring Steel
Heat Mat
WAGO 221-412 x 4
10x3mm Bead x 3
M3x12 Pin x 6

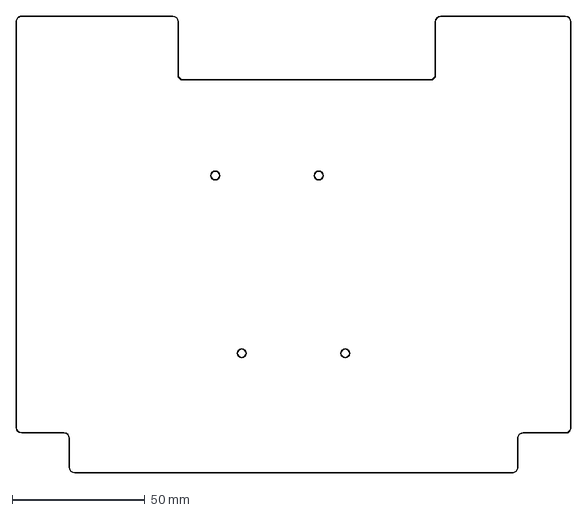
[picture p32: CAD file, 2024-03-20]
DXFs/Deck_Panel/deck_panel_1x_d5_1x_pi.dxf
209.0 x 172.0 mm

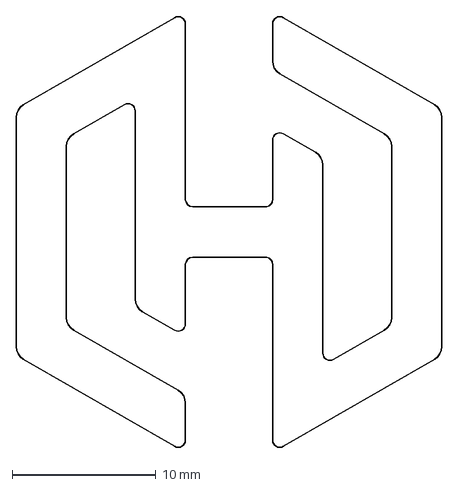
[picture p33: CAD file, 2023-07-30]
DXFs/Logos/Hex-Zero Logo.dxf
29.6 x 30.0 mm

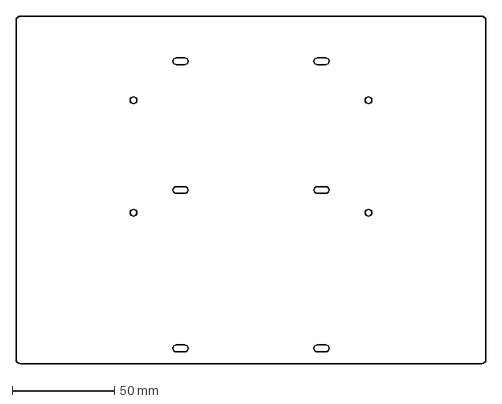
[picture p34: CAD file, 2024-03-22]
DXFs/Mid_Panel/mid_panel_octopus.dxf
230.0 x 170.0 mm

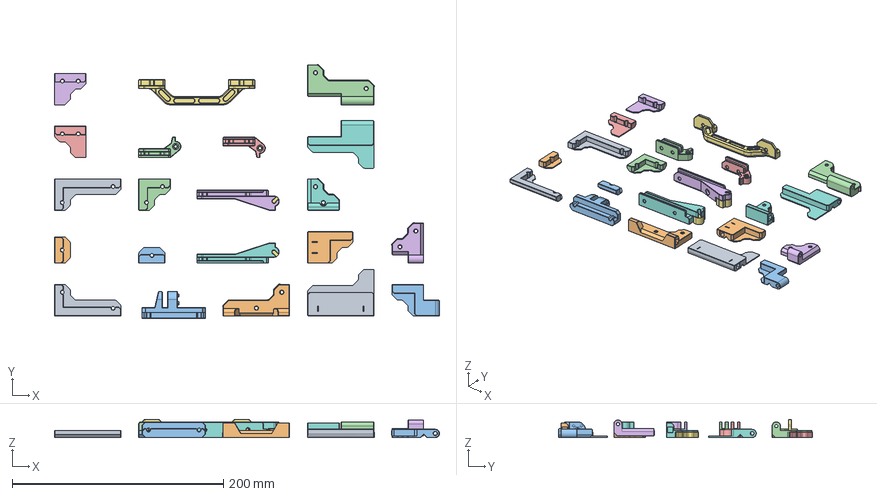
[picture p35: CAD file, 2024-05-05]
Mods/Alexander_T-Moss/3mm_Panel_Clips/CAD/3mm_Panel_Clips.step
364.8 x 240.8 x 17.4 mm
upper_corner_clip_a_2x_3mm
upper_mid_clip_2x_3mm
upper_corner_clip_b_3mm
mid_clip_8x_3mm
corner_clip_17x_3mm
tophat_lower_corner_clip_a_3mm_6x
tophat_lower_corner_clip_b_3mm_6x
side_handle_2x_3mm
upper_door_hinge_a_3mm
front_upper_clip_magnets_3mm
front_corner_clip_magnets_3mm
lower_door_hinge_a_3mm
upper_door_hinge_b_3mm
lower_door_hinge_b_3mm
lower_door_mag_latch_3mm
upper_door_mag_latch_3mm
spool_holder_base_3mm
tophat_hinge_upper_left_3mm
tophat_hinge_upper_right_3mm
tophat_hinge_bottom_left_3mm
tophat_hinge_bottom_right_3mm

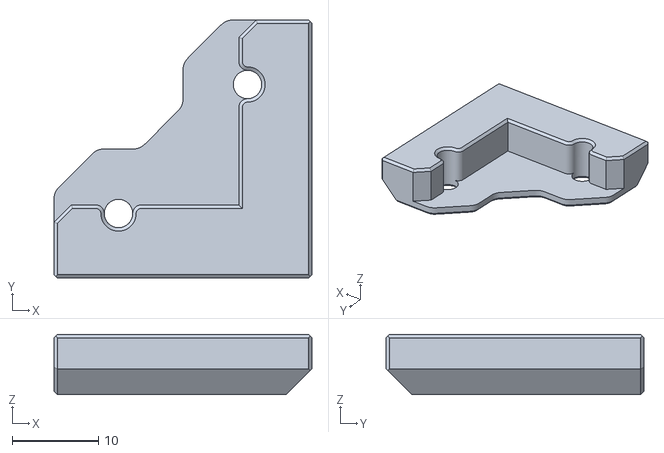
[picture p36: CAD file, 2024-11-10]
Mods/Alexander_T-Moss/3mm_Panel_Clips/STLs/corner_clip_17x_3mm.stl
30.0 x 30.0 x 7.00

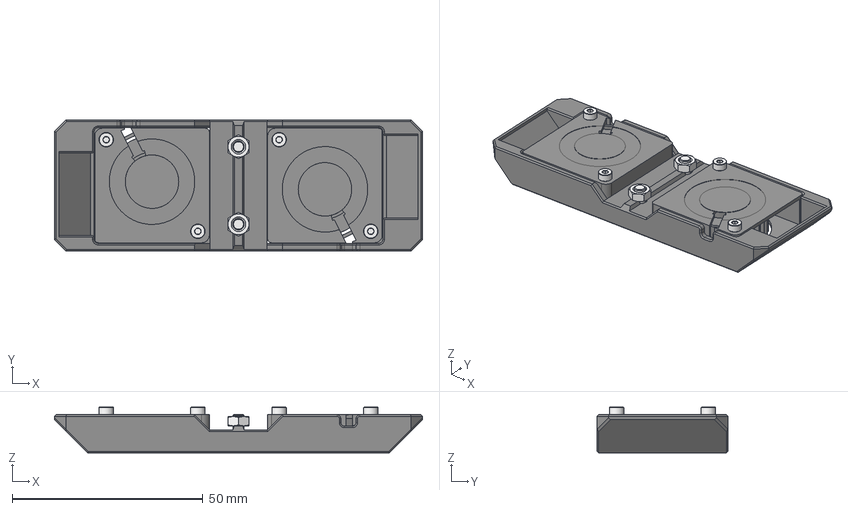
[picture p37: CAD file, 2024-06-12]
Mods/Alexander_T-Moss/Bed_Fans/CAD/Bed_Fans.step
96.4 x 34.3 x 12.0 mm
dual_bed_fan_holder
M3x8 BHCS x 2
M2x10 SHCS x 4
3010 DC Blower Fan x 2
M3 Hexnut x 2

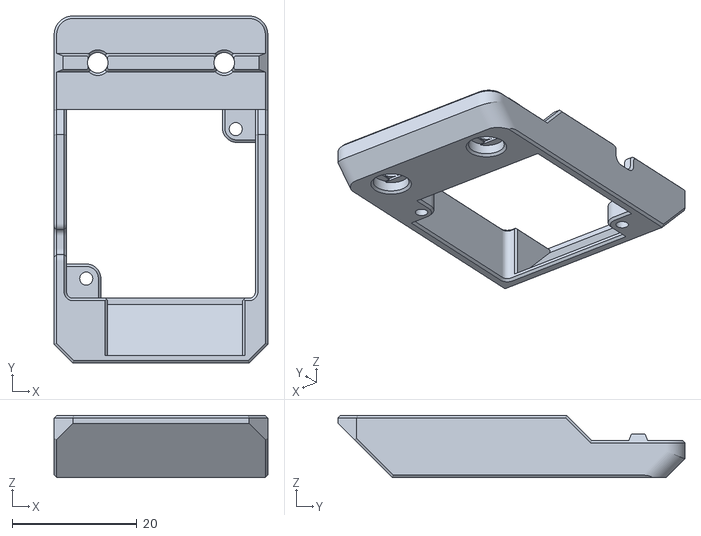
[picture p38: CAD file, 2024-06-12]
Mods/Alexander_T-Moss/Bed_Fans/STLs/single_bed_fan_holder.stl
34.3 x 55.7 x 10.00

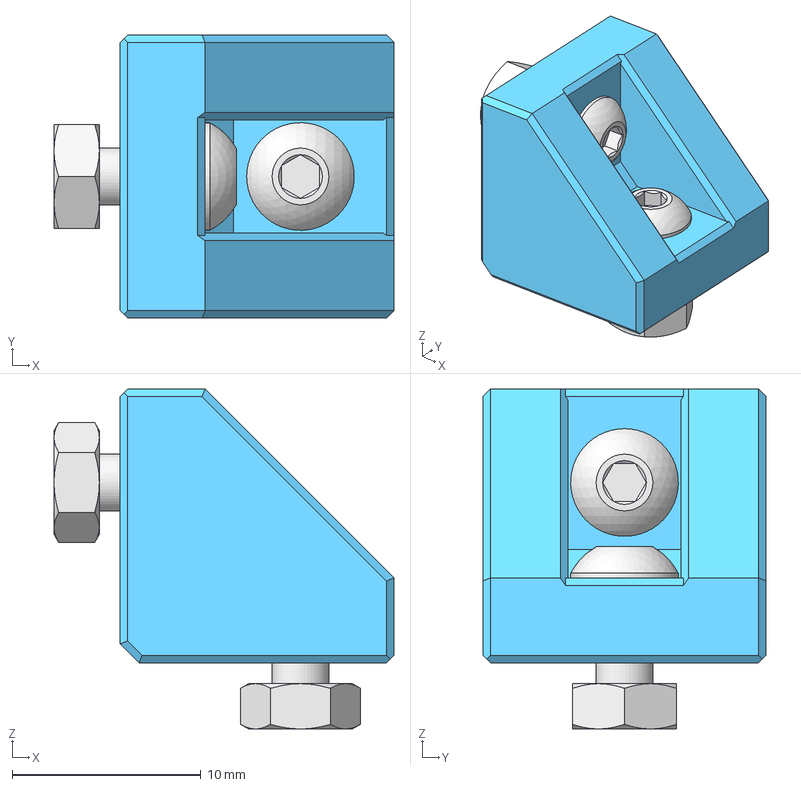
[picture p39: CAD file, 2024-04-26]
Mods/Alexander_T-Moss/Full_Height_Panels/CAD/1515_90_Bracket.step
18.0 x 15.0 x 18.0 mm
M3x8 BHCS x 2
M3 Hexnut x 2
1515_90_bracket

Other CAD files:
Mods/Hoeby/HX0_Anthead/STLs/Main_Bodies/HX0_AntHead_Assembly_v43_main_body_sherpa_x1.stl
Mods/Alexander_T-Moss/Handles/CAD/Handle.step
Mods/Alexander_T-Moss/Handles/STLs/side_handle_2x.stl
Mods/Alexander_T-Moss/Hex_Panels/STLs/hex_mid_panel.stl
CAD/Flying_Beds/Hammer-Head/Hammer-Head_Bed.f3d
CAD/Flying_Beds/Manta-Ray/Manta-Ray_Bed.f3d
DXFs/Deck_Panel/Deck_Panel_2x_Pico_1x_Pi4.dxf
DXFs/Deck_Panel/Deck_Panel_Blank.dxf
DXFs/Deck_Panel/deck_panel_1x_d7_1x_pi.dxf
DXFs/Deck_Panel/deck_panel_1x_skr_e3_1x_pico_1x_pi.dxf
DXFs/Deck_Panel/deck_panel_2x_pico_1x_pi.dxf
DXFs/Deck_Panel/deck_panel_lmf200.dxf
DXFs/Deck_Panel/deck_panel_m5p.dxf
DXFs/Deck_Panel/deck_panel_m8p.dxf
DXFs/Deck_Panel/deck_panel_octopus.dxf
DXFs/Deck_Panel/printable_deck_panel_1x_pico_1x_easybrd_1x_pi.dxf
DXFs/Mid_Panel/Mid_Panel_LMF200.dxf
DXFs/Mid_Panel/mid_panel_lrs_150.dxf
DXFs/Mid_Panel/mid_panel_m8p.dxf
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

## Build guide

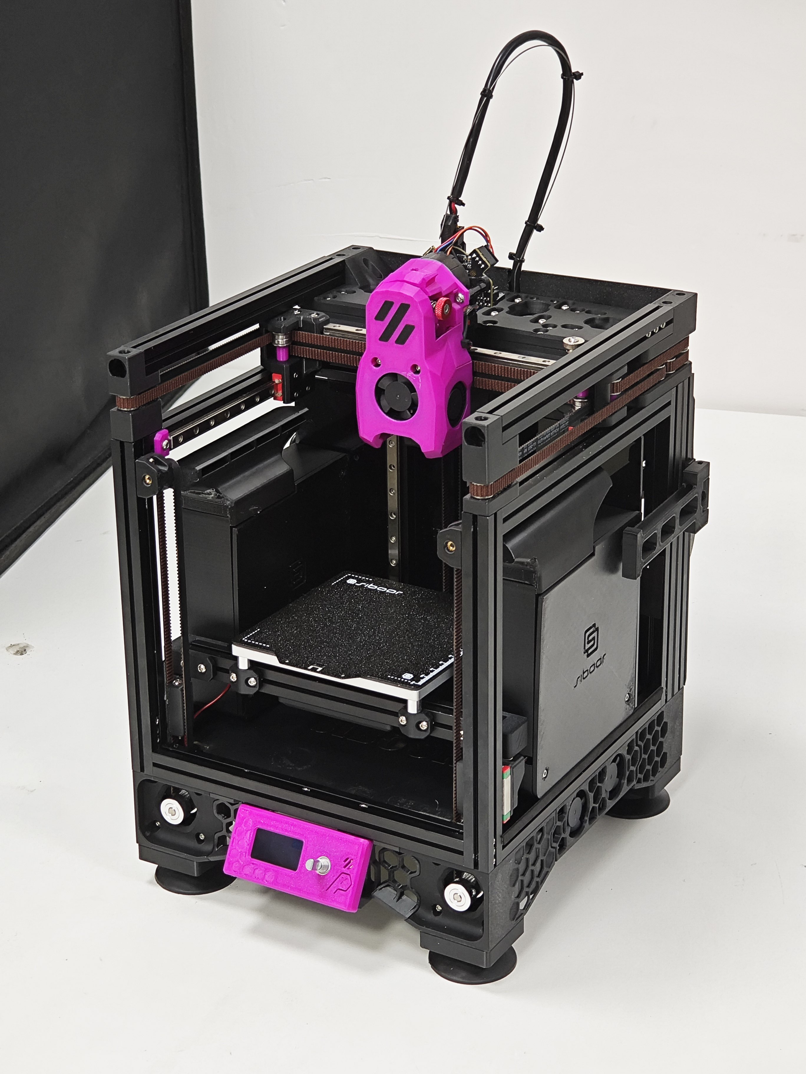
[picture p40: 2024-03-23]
Images/Beta_Tester_Builds/HX0_3.jpg

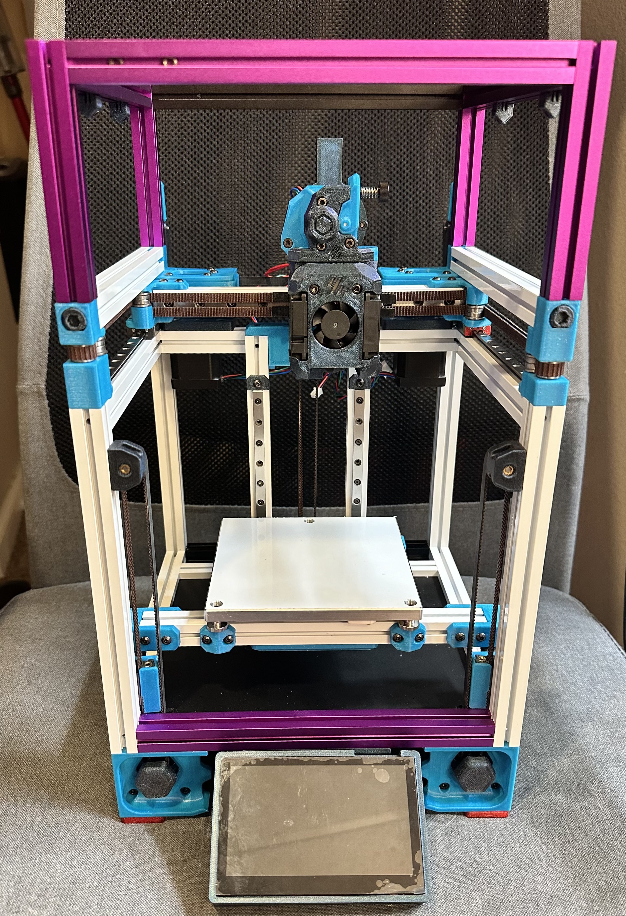
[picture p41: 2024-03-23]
Images/Beta_Tester_Builds/Sidjdosjsid.jpg

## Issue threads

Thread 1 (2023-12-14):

BOM dead link

EricZimmerman, 2023-12-14:
Full bom, spherical bearings

https://www.printyplease.uk/kglm03

Alexander-T-Moss, 2023-12-14:
The issue with the spherical bearings is the vendor I linked to no longer has them in stock, hence the link leading to a product not found page, and also for the extrusions, the compete BOM is more a reference for myself (so I can effectively subtract the V0 BOM from it to get an upgrade BOM)

Alexander-T-Moss, 2023-12-14:
I will look at putting alternative links in the BOM for the bearings in the morning (00:53 local time atm), and will make it more clear on the full BOM about the frame etc.

EricZimmerman, 2023-12-14:
Fair enough. Just looked odd for a fully sourced hex.

On Wed, Dec 13, 2023, 7:52 PM Alexander Þór ***@***.***>
wrote:

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

Alexander-T-Moss, 2023-12-14:
Updated IGUS KGLM-03 Bearing Link and reworded stuff on the full BOM to make it more clear on what it is

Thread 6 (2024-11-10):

Manta M5P Hard Mounting

DerScorbus, 2024-11-10:
I had the DXF file, deck_panel_m5p, lasered.
Is there a holder that you have to print to make it fit? Because the holes don't fit.
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

Alexander-T-Moss, 2024-11-10:
Yes, there is supposed to be a printed mount, but it's got lost when I've updated the repo at some point from the looks of things, so I will find the mount again now and get it uploaded

DerScorbus, 2024-11-10:
Perfect, thank you!

Alexander-T-Moss, 2024-11-10:
So it appears that I've accidently removed all the hard mount printed parts (the ones you need).. oops..., so I've re-uploaded the ones for the M5P (link below) and will upload all the other ones now, good spot!

https://github.com/Alexander-T-Moss/Hex-Zero/tree/main/STLs/Electronics/Control_Boards/BTT_Manta_M5P

Alexander-T-Moss, 2024-11-10:
Uploaded the missing STLs

DerScorbus, 2024-11-10:
The STls you just uploaded to the M5P are no longer there.

Alexander-T-Moss, 2024-11-10:
That's very weird... well I've re-re-uploaded them again so hopefully they don't magically disapear this time haha

DerScorbus, 2024-11-10:
Haha, strange, I'd report back if it happens again

Closed 2024-11-10.

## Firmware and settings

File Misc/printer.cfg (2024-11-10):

# --------- Hex-Zero Example Configuration v15-09-2024 -------- #
#                                                               #
# --- Pre-Flight Check List (READ THIS BIT, IT'S IMPORTANT) --- #
#                                                               #
#  1. Update the [mcu] serial, you may need to define           #
#     multiple MCU's depending on your hardware setup           #
#                                                               #
#  2. Fill out all the empty pin variables, for your            #
#     convenience they are all flagged with the message,        #
#     "# UPDATE PIN INFO", so can be found with ctrl+f          #
#                                                               #
#  3. Make sure the correct thermistor values have been         #
#     defined, flagged with "# CHECK THERMISTOR"                #
#                                                               #
#  4. Update the extruder information to match you relavent     #
#     extruder, flagged with "# UPDATE EXTRUDER"                #
#                                                               #
#  5. Tune the stallgaurd sensitivity for the A/B motors:       #
#     https://www.klipper3d.org/TMC_Drivers.html?h=sensorless   #
#                                                               #
#  6. PID tune the hotend and heat bed:                         #
#     https://www.klipper3d.org/Config_checks.html?h=pid        #
#                                                               #
# ------------------------------------------------------------- #



[include fluidd.cfg]
#[include mainsail.cfg]

[mcu] # serial found running "ls -l /dev/serial/by-id/"
serial: /dev/serial/by-id/<Your MCU ID here>

[printer]
kinematics: corexy
max_velocity: 300
max_accel: 20000


# Motor Configuration ----------------------------------------- # 

# B Motor
[stepper_x] 
step_pin:                                      # UPDATE PIN INFO
dir_pin:                                       # UPDATE PIN INFO
enable_pin:                                    # UPDATE PIN INFO
endstop_pin: tmc2209_stepper_x:virtual_endstop

rotation_distance: 40
microsteps: 128
full_steps_per_rotation: 200

position_endstop: 132
position_max: 132
position_min: -13

homing_speed: 40
homing_retract_dist: 0
homing_positive_dir: True

[tmc2209 stepper_x]
uart_pin:                                      # UPDATE PIN INFO
diag_pin:                                      # UPDATE PIN INFO
run_current: 0.9
interpolate: False
stealthchop_threshold: 999999
driver_SGTHRS: 255


# A Motor
[stepper_y] 
step_pin:                                      # UPDATE PIN INFO
dir_pin:                                       # UPDATE PIN INFO
enable_pin:                                    # UPDATE PIN INFO
endstop_pin: tmc2209_stepper_y:virtual_endstop

rotation_distance: 40
microsteps: 128
full_steps_per_rotation: 200

position_endstop: 123
position_max: 123
position_min: -2
 
homing_speed: 40
homing_retract_dist: 0
homing_positive_dir: True

[tmc2209 stepper_y]
uart_pin:                                      # UPDATE PIN INFO
diag_pin:                                      # UPDATE PIN INFO
run_current: 0.9
interpolate: False
stealthchop_threshold: 999999
driver_SGTHRS: 255



# Front Left
[stepper_z]
step_pin:                                      # UPDATE PIN INFO
dir_pin:                                       # UPDATE PIN INFO
enable_pin:                                    # UPDATE PIN INFO

microsteps: 128
rotation_distance: 32
full_steps_per_rotation: 200

endstop_pin:                                   # UPDATE PIN INFO
position_endstop: 0
position_max: 110 #105 For Hammer-Head

[tmc2209 stepper_z]
uart_pin:                                      # UPDATE PIN INFO
run_current: 0.3
interpolate: False
stealthchop_threshold: 999999


# Rear
[stepper_z1]
step_pin:                                      # UPDATE PIN INFO
dir_pin:                                       # UPDATE PIN INFO
enable_pin:                                    # UPDATE PIN INFO

microsteps: 128
rotation_distance: 32
full_steps_per_rotation: 200

[tmc2209 stepper_z1]
uart_pin:                                      # UPDATE PIN INFO
run_current: 0.3
interpolate: False
stealthchop_threshold: 999999


# Front Right
[stepper_z2]
step_pin:                                      # UPDATE PIN INFO
dir_pin:                                       # UPDATE PIN INFO
enable_pin:                                    # UPDATE PIN INFO

microsteps: 128
rotation_distance: 32
full_steps_per_rotation: 200

[tmc2209 stepper_z2]
uart_pin:                                      # UPDATE PIN INFO
run_current: 0.3
interpolate: False
stealthchop_threshold: 999999


# Bed Configuration ------------------------------------------- #

[heater_bed]
heater_pin:                                    # UPDATE PIN INFO
sensor_pin:                                    # UPDATE PIN INFO
sensor_type: ATC Semitec 104NT-4-R025H42G      # CHECK THERMISTOR

min_temp: 0
max_temp: 120

control: pid
pid_Kp: 69.433
pid_Ki: 1.126
pid_Kd: 1070.171


# Toolhead Configuration -------------------------------------- #

[extruder]
step_pin:                                      # UPDATE PIN INFO
dir_pin:                                       # UPDATE PIN INFO
enable_pin:                                    # UPDATE PIN INFO

heater_pin:                                    # UPDATE PIN INFO
sensor_pin:                                    # UPDATE PIN INFO
sensor_type: Generic 3950                      # CHECK THERMISTOR

rotation_distance:                             # UPDATE EXTRUDER
gear_ratio:                                    # UPDATE EXTRUDER
microsteps: 16

nozzle_diameter: 0.400
filament_diameter: 1.750
min_temp: -5
max_temp: 285


[tmc2209 extruder]
uart_pin:                                      # UPDATE PIN INFO
run_current: 0.6


# Hotend Fan
[heater_fan hotend_fan]
pin:                                           # UPDATE PIN INFO
heater: extruder
heater_temp: 50.0


# Part Cooling Fan
[fan]
pin:                                           # UPDATE PIN INFO


# Further Kinematic Configurartion ---------------------------- #

[z_tilt]
z_positions:
## For Manta-Ray Bed
 -43.5, 13
 60, 126
 163.5, 13

# For Hammer-Head Bed
# -47.5,9.5
# 60, 130.5
# 167.5,9.5

points:
 10,10
 60,110
 110,10

speed: 80
horizontal_move_z: 10
retries: 3
retry_tolerance: 0.02

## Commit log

2023-04-14 Bulk STL Upload
    Upload of initial STLs
    [[a]_a_drive_platform.stl, [a]_a_tensioner_wedge.stl, [a]_b_drive_platform.stl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]
2023-04-14 Added Built In Supports
    [left_z_belt_attachment.stl, right_z_belt_attachment.stl]
2023-04-15 Uploaded Some DXFs
    [Deck_Panel_2x_Pico_1x_Pi4.dxf, Deck_Panel_Blank.dxf, Mid_Panel_LMF200.dxf]
2023-04-15 Uploaded Temp Screenshots
    Screenshots showing the M3 nuts that need preloading
    [lmf200_panel_mount_spacers.stl, skr_pico_pi4_panel_mount.stl]
2023-04-16 Uploaded KGLM-03 Bearing Mounts
    [[a]_ge4c_mount_3x.stl, [a]_kglm03_mount_3x.stl, front_left_gantry_attachment.stl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]
2023-04-18 Uploaded New X Carriage
    [[a]_x_carriage.stl, [a]_x_carriage_adxl.stl]
2023-04-20 Added V0 Display Support
    Uploaded STLs to allow mounting of the V0 display
    [display_left_foot.stl, display_right_foot.stl, front_left_skirt.stl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]
2023-04-25 STL Update
    New bed centre brace and M4 gantry attachments
    [centre_brace.stl, m4_front_left_gantry_attachment.stl, m4_front_right_gantry_attachment.stl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]
2023-05-03 STL Upload
    Uploaded new XY joints and X carriage
    [[a]_x_carriage.stl, xy_joint_lower_left.stl, xy_joint_lower_right.stl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]
2023-05-31 Updated STLs
    Got on top of the STL changes and uploaded all new/changed STLs
    [[a]_a_drive_platform.stl, [a]_a_tensioner_wedge.stl, [a]_b_drive_platform.stl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]
2023-07-28 Uploaded CAD
    [Deck_Panel_2x_Pico_1x_Pi4.dxf, Deck_Panel_Blank.dxf, Mid_Panel_LMF200.dxf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]
2023-07-28 Uploaded Panel Clip STLs
    [corner_clip_17x.stl, door_handle.stl, door_latch_2x.stl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]
2023-07-28 Uploaded XY Axis STLs
    [[a]_a_drive_platform.stl, [a]_a_tensioner_wedge.stl, [a]_b_drive_platform.stl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]
2023-07-30 Uploaded More STLs
    [[a]_front_z_idler_2x.stl, [a]_front_z_pulley_cover_2x.stl, [a]_kglm03_mount_front_2x.stl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]
2023-07-30 Even More STLs!
    [Deck_Panel_2x_Pico_1x_Pi4.dxf, Deck_Panel_Blank.dxf, Mid_Panel_LMF200.dxf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]
2023-08-03 STL Upload
    [[a]_rail_stop_6x.stl, extrusion_hole_drilling_jig_2x.stl, front_z_idler_spacer.stl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]
2023-08-04 New STLs For Flying Bed
    [front_bed_mount_2x.stl, front_left_gantry_attachment.stl, front_right_gantry_attachment.stl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]
2023-08-10 Renamed STLs
    [rear_z_motor_mount_accent_mmu.stl, rear_z_motor_mount_body_mmu.stl]
2023-08-31 Updated CAD
    [easyBrd_rigid_mount.stl]
2023-09-22 STL Updates
    [[a]_a_drive_platform.stl, [a]_a_tensioner_wedge.stl, [a]_b_drive_platform.stl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]
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2023-09-24 Fixed STL Orientation
    [xy_joint_lower_left_bolted.stl, xy_joint_lower_left_pinned.stl, xy_joint_lower_right_pinned.stl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]
2023-12-08 New AB Drive STLs
    No fundamental changes, just QOL improvements
    [[a]_a_drive_platform.stl, [a]_a_tensioner_wedge.stl, [a]_b_drive_platform.stl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]
2023-12-09 New STLs
    Uploaded latest gantry STLs, including new [a]_x_carriage that uses square nuts instead of hex nuts
    [[a]_x_carriage.stl, [a]_x_carriage_hex.stl, [a]_x_carriage_square.stl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]
2023-12-09 New STLs
    Updated XY Idler STLs
    [[a]_tophat_locker_2x.stl, xy_left_idler_lower_bolted.stl, xy_left_idler_lower_pinned.stl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]
2023-12-09 New STLs
    Updated Motor Mounts. Now Include Feet Mounting Option
    [Rear Z Motor Mount MMU.step, [a]_front_z_pulley_cover_2x.stl, [a]_logo_accent.stl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]
2023-12-10 RC1 STL Upload
    [[a]_a_drive_platform.stl, [a]_a_tensioner_wedge.stl, [a]_b_drive_platform.stl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]
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2023-12-23 Improved Supports
    Updated built in supports on parts
    [left_z_belt_attachment.stl, rear_z_idler.stl, right_z_belt_attachment.stl]
2024-01-20 RC1.1
    Renamed some folders to remove spaces, uploaded the remaining printed jigs and moved them (along with existing) into their own folder
    [Rear Z Motor Mount MMU.step, [a]_a_drive_platform.stl, [a]_a_tensioner_wedge.stl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]
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2024-03-20 Deck Panel Electronics Mounting
    [btt_octopus_hard_mount_2x.stl, btt_octopus_vhb_mount_2x.stl, deck_panel_1x_d5_1x_pi.dxf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]
2024-03-22 New Mid Panel DXFs
    [mid_panel_lrs_150.dxf, mid_panel_m8p.dxf, mid_panel_octopus.dxf]
2024-04-13 Fixed STL Orientations
    [[a]_kglm03_mount_front_2x.stl, [a]_kglm03_mount_rear.stl, [a]_left_z_belt_tensioner.stl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]
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2024-04-24 Spool Holder Fix
    [3mm_Panel_Clips.f3d, 3mm_Panel_Clips.step, spool_holder_base.stl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]
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2024-05-08 Added Some DIN Clips
    [btt_octopus_hard_mount_2x.stl, btt_octopus_vhb_mount_2x.stl, easyBrd_rigid_mount.stl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]
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2024-06-12 File Reorg For Hammer-Head Bed
    [[a]_kglm03_mount_front_2x.stl, [a]_kglm03_mount_rear.stl, centre_brace.stl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]
2024-06-12 Add Bed Fans Mod
    [Bed_Fans.f3d, Bed_Fans.step, dual_bed_fan_holder.stl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]
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2024-06-13 Fixed Names
    [Deck_Panel_Logo_MMU.step, Deck_Panel_MMU.step, Hex_Mid_Panel_MMU.step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]
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2024-06-22 New Files And Restucture
    [Hammer-Head_Bed.f3d, Manta-Ray_Bed.f3d, Manta-Ray_Bed.step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]
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2024-07-25 Fix folder structure
    [Hex-Zero_Wago.step, Hex-Zero_Wago.stl]
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2024-09-10 Missing STL
    [corner_clip_17x_3mm.stl]
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2024-09-17 Fix cowl_zeroclick support
    [cowl_zeroclick.step, cowl_zeroclick.stl]
2024-11-10 Upload Missing STLs
    [manta_m5p_hard_mount_a.stl, manta_m5p_hard_mount_b.stl]
2024-11-10 Re-re-Upload Missing STLs
    [manta_m5p_hard_mount_a.stl, manta_m5p_hard_mount_b.stl]
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2024-12-31 STL Revision
    Revised front z belt tensioner blocks
    [[a]_left_z_belt_tensioner.stl, [a]_right_z_belt_tensioner.stl]
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2025-01-26 Update and rename HX0_Mantaray_bed.stl to HX0_Mantaray_bed_error.stl
    [HX0_Mantaray_bed_error.stl]
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2025-02-08 Added Hex-Burner Revo PZ Mod
    [Hex-Burner_Revo_PZ_Sherpa_Mount.step, Hex-Burner_Revo_PZ_Sherpa_Mount.stl, X-Carriage_Revo_PZ_Board_Mount.stl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]
2025-02-08 Missing revo pz sherpa mount picture and typos
    [X-Carriage_Revo_PZ_Board_Mount_with_Bumper.stl]
2025-02-08 Added Hex-Burner offset carriage mod
    [Hex-Burner_Revo_PZ_Sherpa_Mount.step, Hex-Burner_Revo_PZ_Sherpa_Mount.stl, X-Carriage_Revo_PZ_Board_Mount.stl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]
2025-02-08 Added top hat brace mod
    [top_hat_corner_brace.step, top_hat_corner_brace.stl, top_hat_corner_brace_with_offset.step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]
2025-02-08 GBB15 motor panel mod
    [gbb15_motor_panel_mount.step, gbb15_motor_panel_mount.stl]
2025-10-19 add 48mm z motors usermod
    [left-side-skirt.stl, right-side-skirt.stl, z-mount-back.stl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]
